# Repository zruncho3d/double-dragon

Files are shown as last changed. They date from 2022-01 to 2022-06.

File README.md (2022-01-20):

# Double Dragon

a Voron Zero mod to add Independent Dual Extrusion (IDEX).  "X0" for short.  **Now printing!**

**X0** adds a second printhead to a [V0](https://vorondesign.com/voron0.1) to enable multi-color prints, multi-material prints, and even overhangs atop dissolvable supports.  

*This repo includes everything you need to build your own X0, including CAD and STLs for printed parts, DXFs for panels, a list of parts, and a sample Klipper config.*  The .STEP file is now in the repo too.

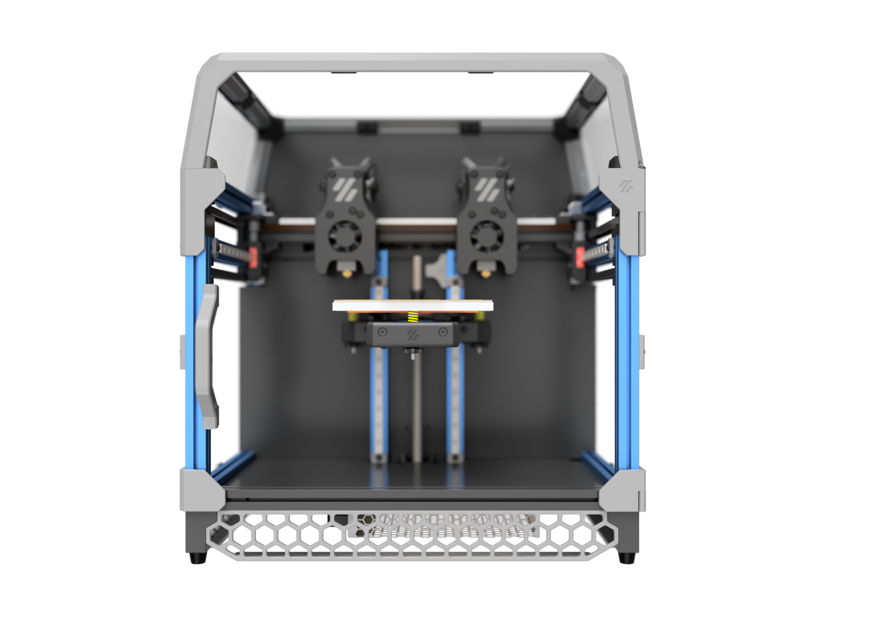
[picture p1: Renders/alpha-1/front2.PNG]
front


## Updates
* **2022-01-02** First multi-extruder prints!  See the alternating-copper-and-brass print below.
* **2022-01-01** See [this Reddit discussion](https://www.reddit.com/r/VORONDesign/comments/ru64ti/idex_v0_bad_idea_or_terrible_idea/) for reactions to the concept: bad idea, or terrible idea?
* **2021-12-31** Initial alpha-1 release!  This one was fun.  Came together quickly, too.

## Alpha-1 Release 2021-12-31

front

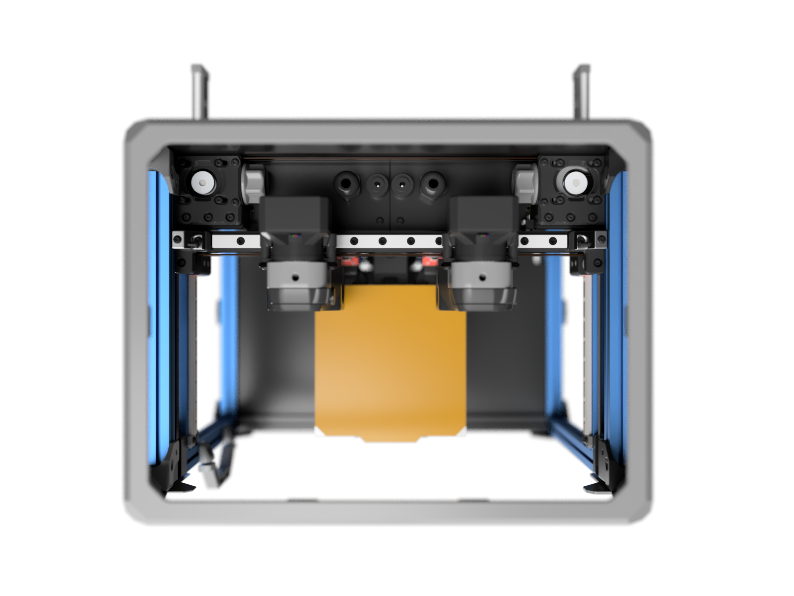
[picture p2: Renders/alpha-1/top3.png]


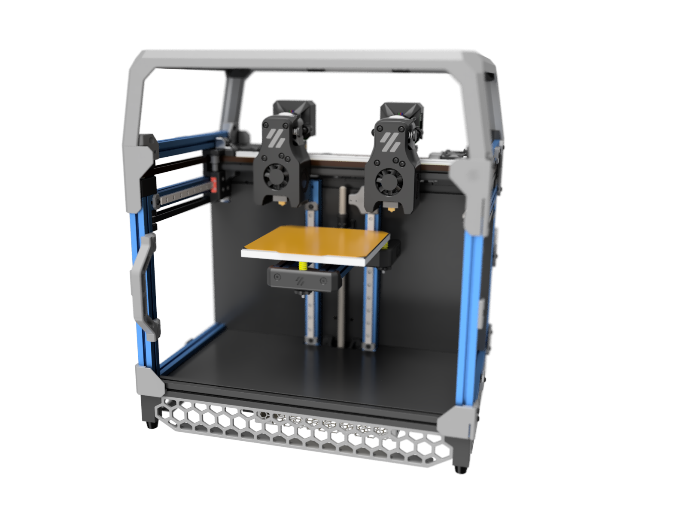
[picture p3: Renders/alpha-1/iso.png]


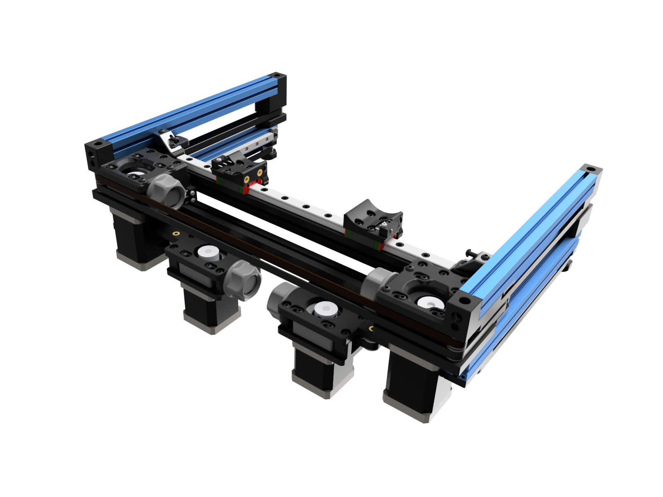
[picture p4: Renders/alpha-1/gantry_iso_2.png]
gantry iso


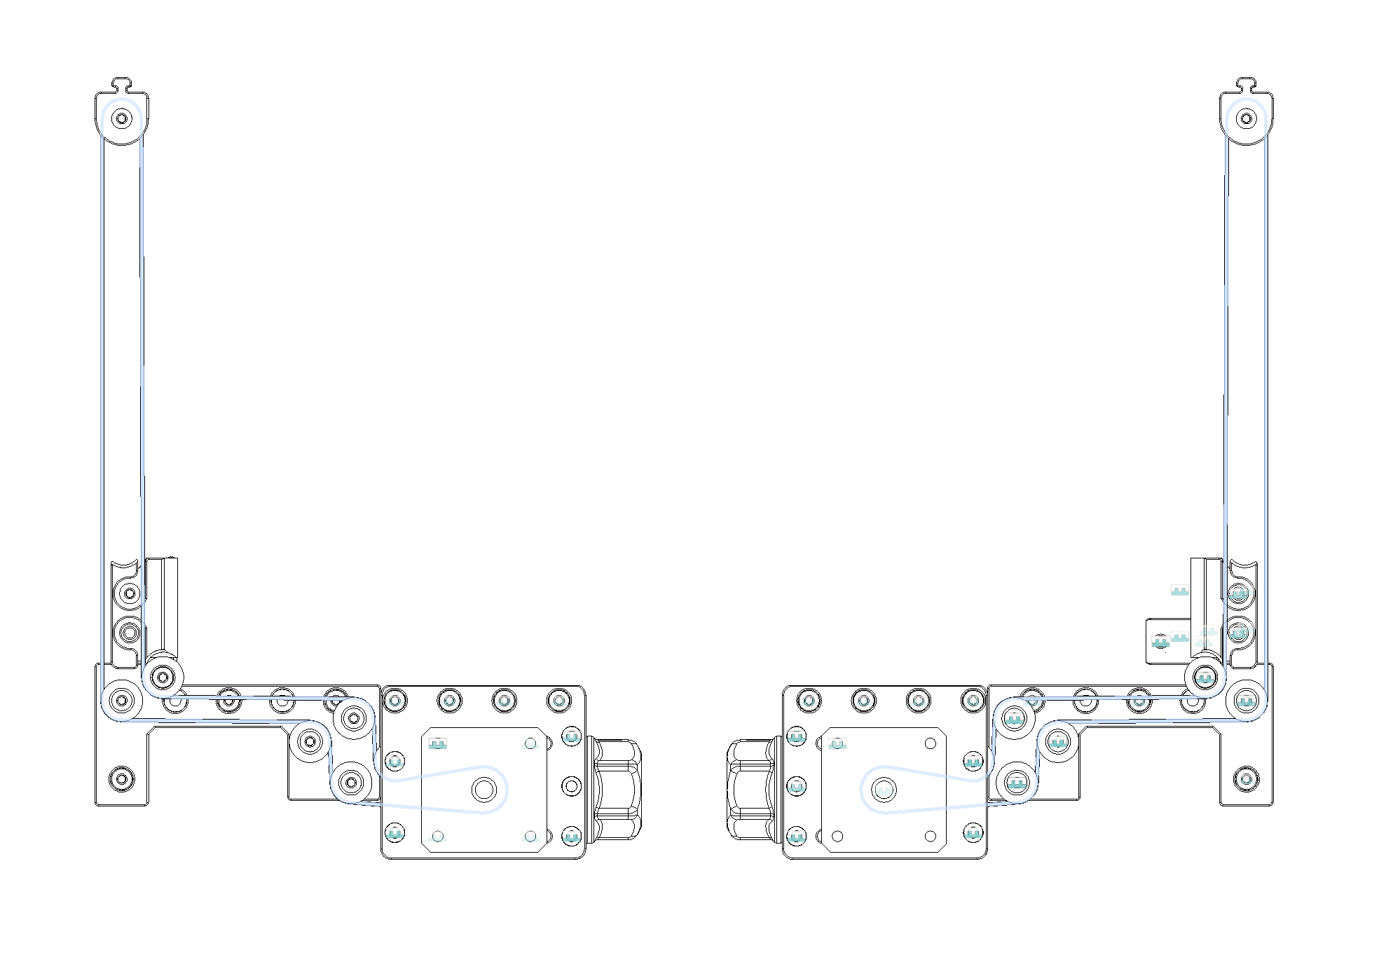
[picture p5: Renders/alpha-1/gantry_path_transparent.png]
gantry path


### Yes, it's real, and yes, it prints.  X0.000 in progress:

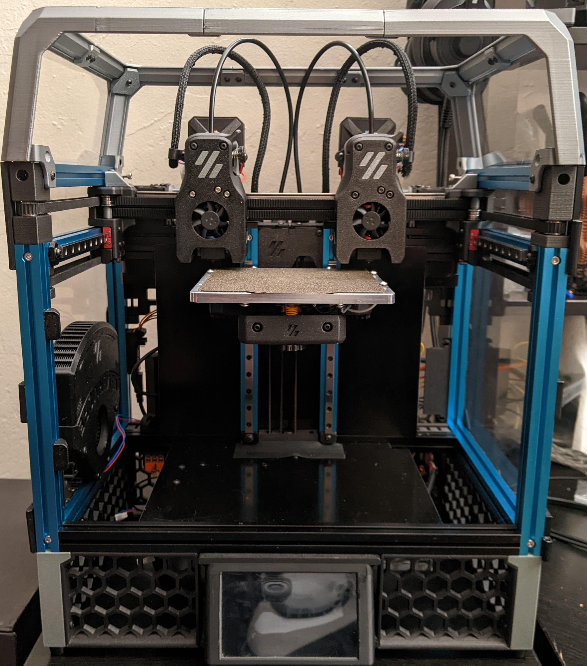
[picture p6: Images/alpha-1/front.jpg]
front


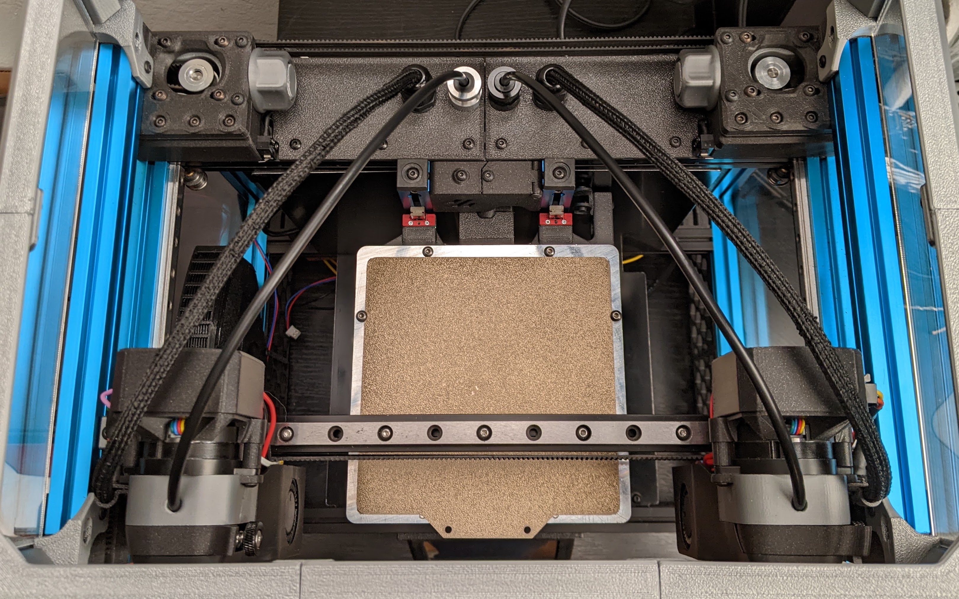
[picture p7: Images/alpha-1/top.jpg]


Sample print with two extruders in one part, with brass and copper PLA.

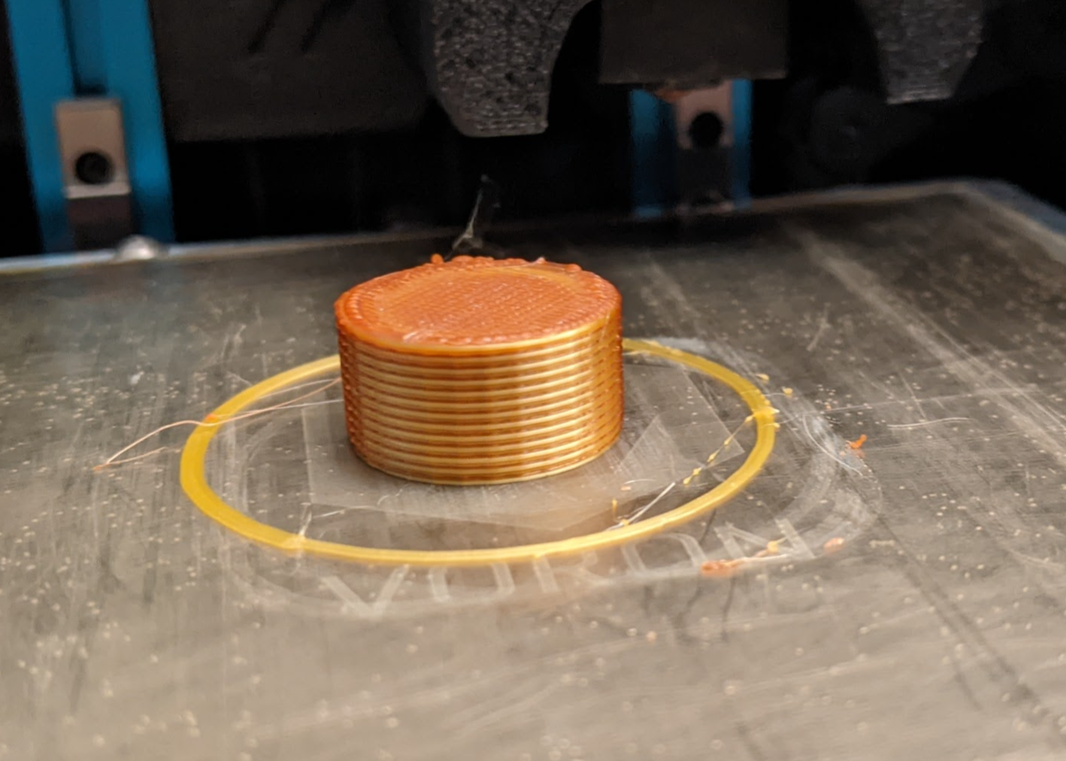
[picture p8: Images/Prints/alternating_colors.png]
alternating


Videos coming soon.

### Fun parts

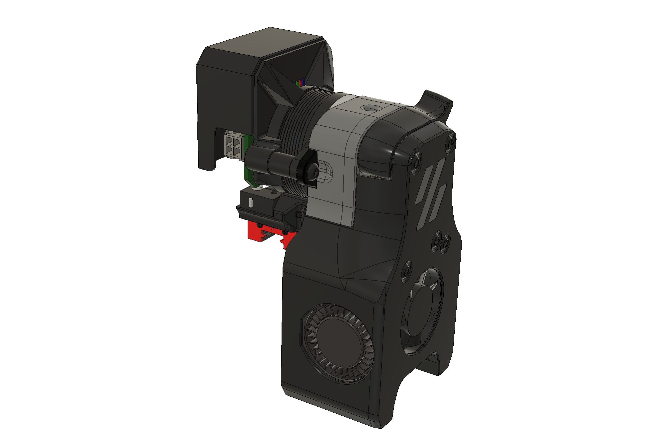
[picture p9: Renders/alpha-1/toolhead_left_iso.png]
Toolhead


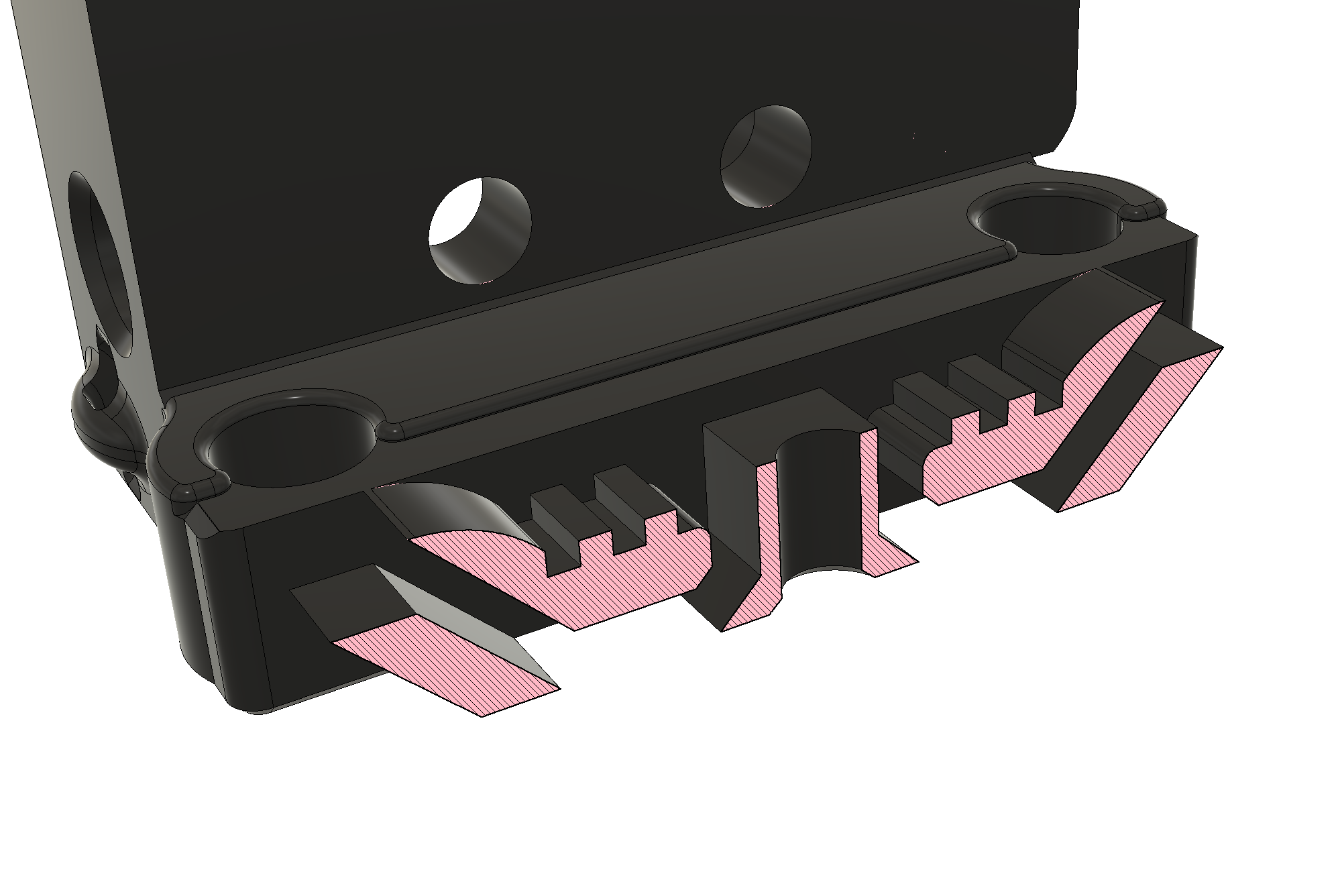
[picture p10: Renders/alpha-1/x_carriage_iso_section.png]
X Carriages iso section


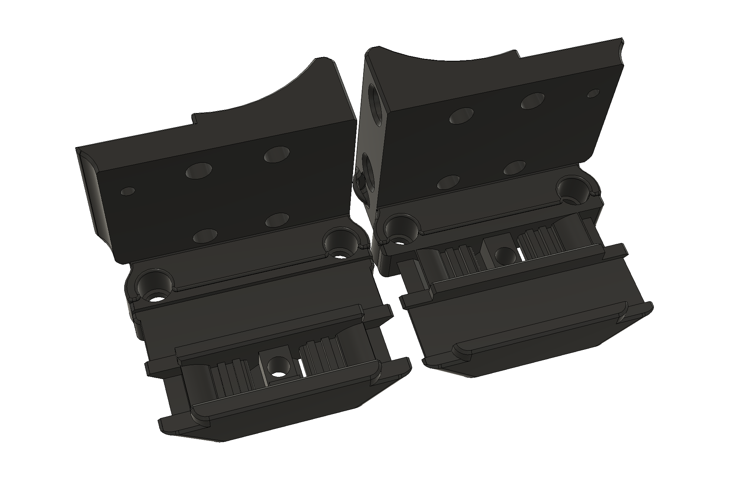
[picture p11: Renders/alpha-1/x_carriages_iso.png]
X Carriages iso


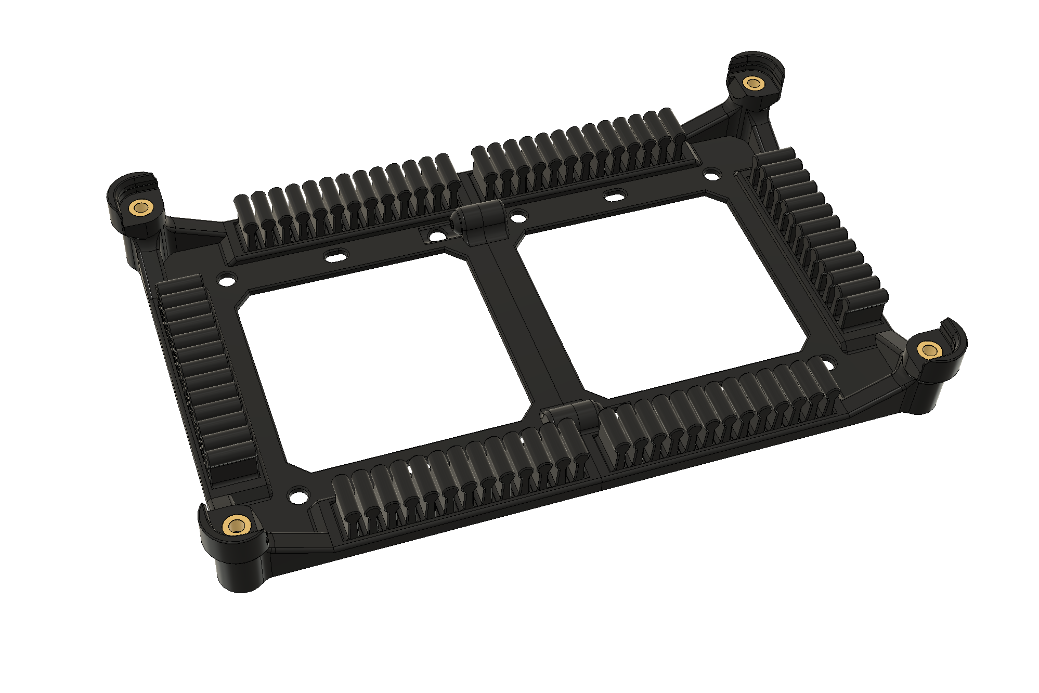
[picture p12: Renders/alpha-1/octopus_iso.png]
Octopus iso


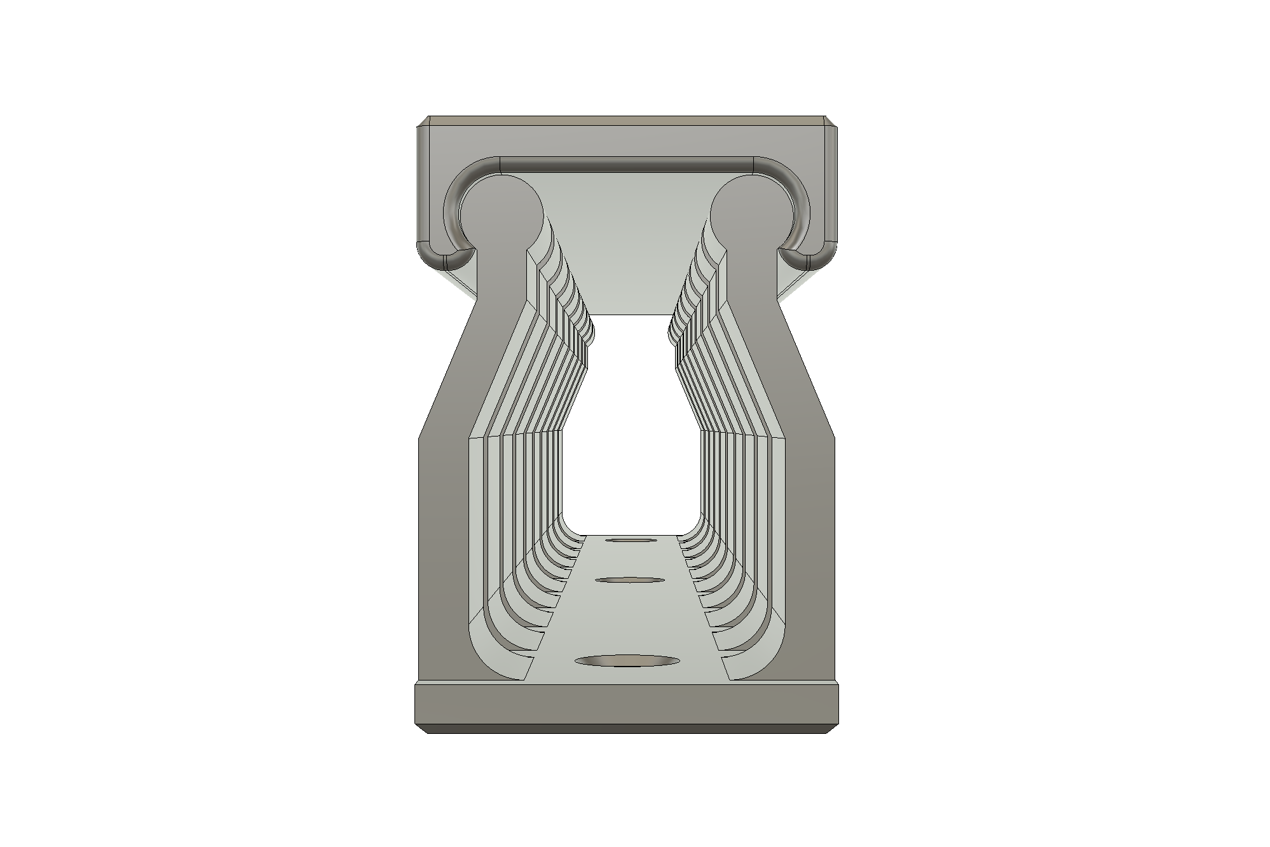
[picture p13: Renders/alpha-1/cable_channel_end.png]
Cable Channel End


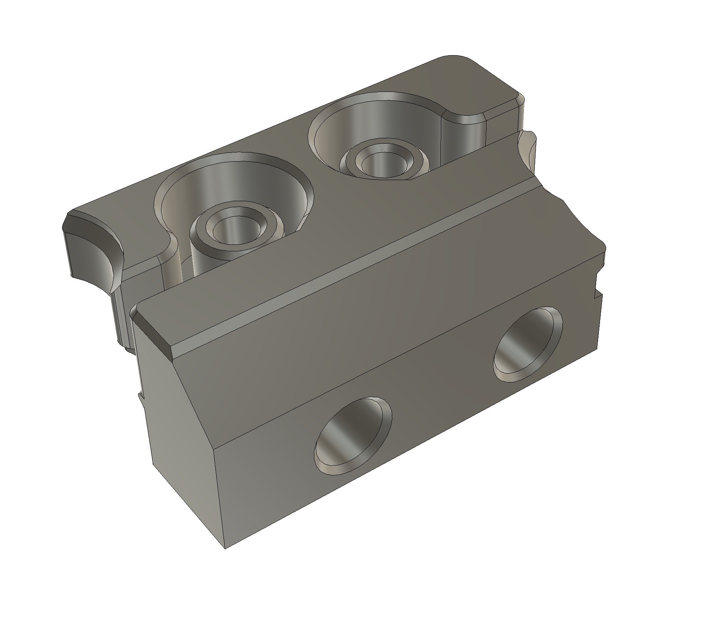
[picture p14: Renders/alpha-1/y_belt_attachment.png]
Y Belt Attachment


## I'm interested. What do I need to do?

Take a V0, then..

#### Double up the toolheads
You'll need a second toolhead.
* A default [V0.1 Mini Afterburner toolhead](https://github.com/VoronDesign/Voron-0/tree/Voron0.1/STLs/Toolheads/Mini_Afterburner) works fine, but anything V0-X-carriage-compatible will work too, like the [Mini AfterSherpa](https://github.com/KurioHonoo/Mini-AfterSherpa), which has some nice features.
* Toolhead boards are highly recommended, whether with-chip like the [Huvud](https://github.com/bondus/KlipperToolboard) or chip-less ([Pancake Board](https://github.com/christophmuellerorg/voron_0_pancake_board), [Timmit's V0 Umbilical](https://github.com/VoronDesign/Voron-Hardware/tree/master/V0-Umbilical), …).
* Anything that changes the X carriage will NOT work, such as the [Mini After-LGX-lite](https://www.bondtech.se/2021/12/27/voron-v0-1-toolhead-setup-for-lgx-lite/), at least until any changes are ported over.

#### Widen all the things!
* **100mm-wider extrusions** - 4x 300mm; [MakerBeamXL](https://www.amazon.com/MakerBeam-XL-Anodized-300x15x15mm-Pieces/dp/B06XJ5G5QY), Misumi, or whatever you prefer.  Or, keep the colorful extrusions from a kit and augment with 8x 50mm extensions, joined by M3 threaded rods, 3mm shafts, or long M3 screws.
* **100mm-longer X rail (250mm)** - a medium preload MGN9 rail with two MGN9C carriages is recommended, as it reduces the potential for toolhead wobble.  Ask the seller for medium preload at purchase time and ask them to put both carriages on the rail.  Make sure to order two carriages!  [CNA rail and carriages on AliExpress](https://www.aliexpress.com/item/32773296501.html?spm=a2g0s.12269583.0.0.4ea2494dwPIVR2)
* **100mm-plus wider bed (optional)** - see notes below.
* **100mm-wider panels (optional)** - see DXFs folder and image below.  You can ignore these if the printer is unenclosed, or you can make printed 50-mm-wide shim parts, possibly with a nice accent color.  The tophat panels are a bit harder to extend, but you could shim these too, potentially.
* **100mm-wider skirts (optional)** - this repo includes a 100mm hex skirt to match the [default V0.1 skirts](https://github.com/VoronDesign/Voron-0/blob/Voron0.1/STLs/Skirt_x3.STL). X0.000 above has custom 70mm skirts to fit a [4" touchscreen mod](https://github.com/Fleafa/VoronUsers/tree/V0.1-Trident-skirt/printer_mods/roboticator24/4inch_touchscreen_mount_for_v2.4) for [KlipperScreen](https://github.com/jordanruthe/KlipperScreen).  But again, use what you like, such as [MCMBen's Trident-style skirts](https://github.com/Fleafa/VoronUsers/tree/V0.1-Trident-skirt/printer_mods/MCMBen/Voron0_Trident_Skirt), which nicely integrate the mini V0 display you may already have.

The panel order looks like this, from SendCutSend:

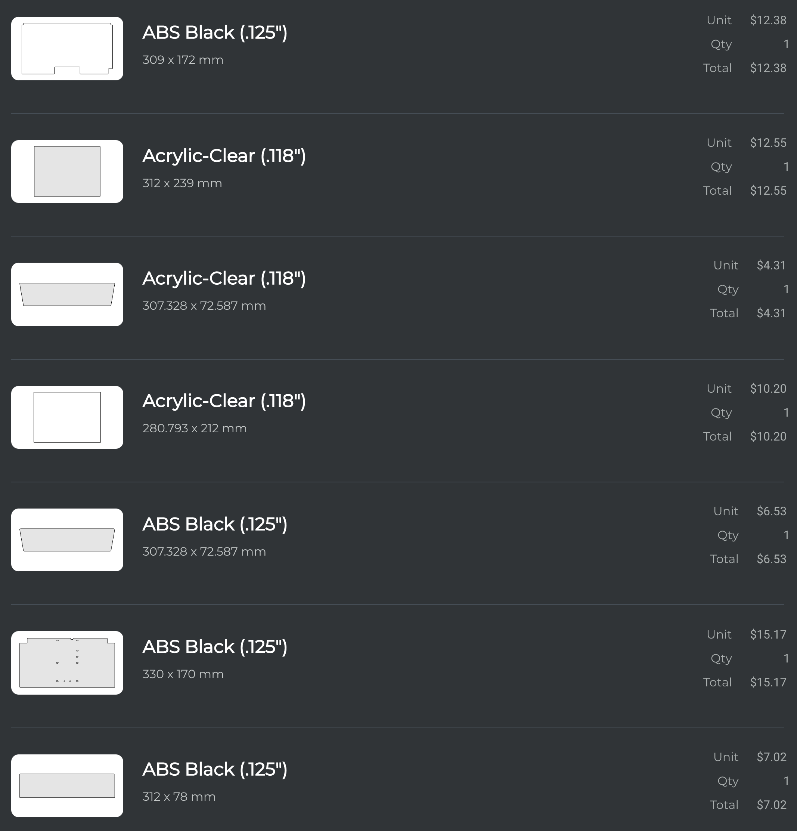
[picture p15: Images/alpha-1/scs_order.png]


#### Add more drives!
This mod uses two Y motors for simplicity in a `hybrid-corexy` config.  You'll need:
* **Belts**: +N 6mm-width GT2 belt; can reuse your now-too-short belts on the Y drives.
* **Pulleys**: +2 20-tooth GT2
* **Endstops**: +2 Omron D2F switches
* **Bearings**: +28 F623 bearings (sorry for the number... had to fit the existing V0 footprint)
* **Motors**: +2 NEMA14 for the Y drives.  If using full-length 48mm+ motors, an Octopus will not fit the provided mount, but a Spider will.  V0.0-stock motors are shorter and will fit.
* **M3 Screws**: Yes, all BHCS; includes at least M3x6, M3x8, M3x10, M3x12, M3x16, M3x20, M3x25.
* **M3 Nuts**: Yes
* **M3 Heatsets**: Yes
* **M3 Washers**: Yes

Note, parts above are *just* for drives, not for the toolhead.  Those will add to the bill of materials.

Also: **additional stepper driver ports**.  Octopus, Spider, Fly, GTR, S6, 2x SKR Mini/Pico, … Klipper doesn’t care.  Use whatever you’ve got that gives you added ports.  You need an extra 2 stepper ports for Y motion and one extra stepper port for the second extruder, unless you go with a toolhead board.

#### More power!!!  

The extra power draw of three more steppers, plus an extra toolhead heater, **absolutely** requires a more capable power supply than a stock V0, whether 100W for an AC bed or 150W for a DC bed.  DO NOT run without known margin.  If you're not sure, buy or borrow an inline power meter to confirm.

A second power supply or larger one both will work fine.  The good news is that you have 100mm additional width to fit it below the main deck panel.

Consider a UHP200, dual LRS-100-24 units (what I use), an LRS-350-24 if you don't mind occasional fan noise, an LRS-150-24 with an AC bed, or really, anything else.

There’s no BOM yet, because there’s only two new parts for the BOM - the longer rail and the longer extrusions.

#### Printed parts (required)

Most of the bigger parts are *fully reused* from a V0.  That’s kinda the point here… take a V0 and make it an IDEX with the fewest modifications possible.  That includes the toolhead, AB blocks, front idlers, top gantry parts, and enclosure parts.

What remains?  You’ll need a few new parts, plus a few copies of existing V0 parts.  But surprisingly, not that much.  Everything is printable on the 120x120 bed of a V0.

| Category | Part | Qty | Notes |
| - | - | - | - |
| X Gantry | ```XY_Joint_Lower_Extended``` | 1 + 1 | Enables attachment to Y belt blocks |
| | ```X_Endstop``` | 1 + 1 | Enables tightening + tensioning without screw interferences |
| | ```X_Carriage``` | 1 + 1 | Needed to support belt passthrough for hybrid-corexy layout; leaves extra belt around, so it improves the experience of tightening/retightening |
| Y Drives | ```Y_Belt_Attachment``` | 1 + 1 | Perfect fit with the Y drive pulleys to enable 120mm Y travel
| | ```Y_Front_Idler_Mount``` | 4 | Spaces and retains Y front idler bearings |
| | ```Y_Bearing_Plate``` | 1 + 1 | Holds bearings to route the belts |
| | ```Y_Drive_Frame_Upper``` | 1 + 1 | Shortened and modified V0 part |
| | ```Y_Drive_Frame_Lower``` | 1 + 1 | Shortened and modified V0 part |
| | ```Y_Drive_Tensioner``` | 2 | Shortened and modified V0 part |
| | ```Tensioner_Knob``` | 2 | [Extra of a stock V0 part](https://github.com/VoronDesign/Voron-0/blob/Voron0.1/STLs/%5Ba%5D_Tensioner_Knob_x2.stl) |
| Misc | ```Spool_Holder``` | 1 | [Extra of a stock V0 part](https://github.com/VoronDesign/Voron-0/blob/Voron0.1/STLs/Spool_Holder_V0_x1.STL) |

#### Printed parts (modified)

The left-side AB block needs one modifiecation: to drill two sub-2mm holes in the existing part to match the other side, then use 2x self-tapping M2 screws to attach it.

#### Printed parts (optional)

| Category | Part | Qty | Notes |
| - | - | - | - |
| Wire Management | ```Separator``` | 1 + 1 | Full-width covers to connect toolhead to [cable glands](https://www.amazon.com/gp/product/B077R1RT2T) and reverse bowden tubes
| | ```Reverse_Bowden_Clip``` | 2 | Clamps to a 4mm bowden tube and mounts to Dragon groovemount
| | ```Cable_Channel_100mm_15x22_Base``` | 3 | Keep those wires organized
| | ```Cable_Channel_100mm_15x22_Cover``` | 3 | Keep those wires organized
| | ```Octopus mount base``` | 2 | Rotationally symmetric part to hold Octopus
| | ```Wire_Fingers``` | 6 | Clips into Octopus mount, but also usable with a piece of VHB tape below
| Tophat | ```Tophat_Middle_Spacer``` | 2 | Widens tophat by 100mm
| | ```Front_and_Rear_Midclip``` | 2 | [Extra of a stock V0 part](https://github.com/VoronDesign/Voron-0/blob/Voron0.1/STLs/Tophat/Front_and_Rear_Midclip_x2.STL)
| Skirts | ```Skirt_Center``` | 1 | Matches stock V0.1 front skirts

See also toolhead parts in the ```Huvud_Toolhead``` folder.  Quantities for those parts assume you go for 2.

All parts should be printed at standard Voron settings (4 perims, 40% infill, 5 top / 5 bottom layers) except for:
* ```Wire_Fingers```: use 2 perims, 0% infill, 0 top / 0 bottom layers - they’re meant to be flexible loops
* ```Tophat_Middle_Spacer```: use 0.16 layers, as the overhangs are significant

All parts should already be in print-ready orientation, where the seam is assumed to be at the back (+Y).  

No supports are necessary for any parts.

### Software. How?

X0 uses a stock mainline Klipper with minimal changes.  Duplication and mirroring may require extra patches; those are currently untested.  There’s a sample Octopus config in the repo.  The key changes to Klipper config are to define a second Y drive and use ```[dual_carriage]``` to define a second X drive.

Also, make sure your slicer outputs T0 and T1 commands; for SuperSlicer, select the Marlin type, not Klipper type.  The easiest way to test this is to right-click the bottom right of the slicer view in SuperSlicer and have it do a pattern of alternating extruders.  You’ll need to have the two extruders configured too, but they should be identical.

### Calibration.  How?

Great question.  Welcome to the bleeding edge.  It’s sharp.

The best guide I’ve seen is this [guide](https://github.com/Klipper3d/klipper/pull/4508/commits/f2cfa7021d2f2079829e65b9544e9c80def937d6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) from charlespick on Github.
You print test patterns to align the two toolheads in X and Y, then test until Z is right.  Here’s a sample.

### What part size can I print?

Good question.

If you keep a V0 120x120 bed, then _most_ of the V0 printable size remains.  The V0.1 MiniAB is 53mm and the added travel is 50mm… so one carriage would hit the other at 3mm from the build-plate edge.  That means you can print a single part with two materials or colors, up to 114mm in X and ~120mm in Y.  Great!

But remember: toolheads can’t touch.  So in mirror mode (which requires toolhead height adjustment; not implemented yet), you lose that 53mm between nozzles, yielding 2 parts at 33.5mm x 120mm.  In Duplication mode, you get the space divided by two, up to the toolhead edge - 60mm x 120mm for each part.  Much better.

But what if you go with a larger bed?

You can print much wider, and that changes the utility of your V0 in a big way.   Assume a 100mm-wider 220mm bed width, or more.  In mirror mode, you lose 53mm again, so you get 2x 83.5mm x 120mm [(220.0 - 53)/2].  Much better.  In Duplication you get the space divided by two - 110mm x 120mm for each part.

That's pretty good.  That's why toolhead height adjustment would be a great improvement.

### Can I use [insert V0 mod here]?

Maybe.  

The Double Dragon mod is compatible with many Z mods for V0, including [Tri-Zero](https://github.com/zruncho3d/tri-zero) for automatic bed leveling, as well as various belted Z conversions, including:
*  MCMBen's  [Block-and-Tackle Z](https://github.com/Fleafa/VoronUsers/tree/master/printer_mods/MCMBen/Voron0_Block_and_Tackle_Z_Belt/STLs)
* nhchiu's [Movable Pulley Z](https://github.com/nhchiu/VoronUsers/tree/pulley_z/printer_mods/nhchiu/V0.1_Movable_Pulley_Z)
* theFPVgeek's [belted Z mod](https://github.com/theFPVgeek/VoronUsers/tree/master/printer_mods/theFPVgeek/v0-zbelt-mod)
* MathematicalPotato's [V0.1 mod of theFPVgeek's mod](https://github.com/VoronDesign/VoronUsers/tree/master/printer_mods/MathematicalPotato/v0.1_belted_z_drive)
* ... and more

Lights on top should be fine.  Tophat lifters may need some extensions for the added width.  Also, the Y belts below the side extrusions might get in the way of some mods though, so watch out.

###  What’s left to do?

Lots of stuff.  You’ve got the CAD.  Have at it.  

Here’s a starter list of useful contributions.  PRs welcome!
* Mechanical nozzle height adjustment on the toolhead; required to do mirror and duplicate modes correctly.
* Purge bucket
* Nozzle scrubber
* Narrower toolhead for more usable X
* Calibration assists
* Printable rear separator parts to fit the 14-pin connectors of no-chip toolhead boards
* Printable panel extensions

### Questions.  Where?

Project development and updates live in the ```#double-dragon``` channel in the [DoomCube Discord](https://discord.gg/doomcube).

Feel free to report issues as GitHub issues!  Makes them easier to track.

**What am I seeing in the pictures?  That doesn't match the CAD.**

Good eye.  You can modify a stock V0.1 with the mods listed above and you'll see something like the renders, but the images are a bit different.

X0.000 in the pics has a few tweaks to a stock V0.1, in addition to Double Dragon-specific mods:

* MCMBen's [Block-and-Tackle Z for V0](https://github.com/Fleafa/VoronUsers/blob/master/printer_mods/MCMBen/Voron0_Block_and_Tackle_Z_Belt/STLs/%5Ba%5D_tensioner_v1.stl)
* 2x Custom Rotating Spool holders
* 2x Huvud mounts for small NEMA17 motors, with custom cable clips, plus connectors to pass 5V to the MiniAB fan.  Only 5 wires each.
* 2x Repurposed Dragon groovemount adapters for bowden tubes
* Custom 70mm skirts to fit a 4" touchscreen mod for KlipperScreen
* FUNCORE [accessible-screws V0.1 frame](https://www.aliexpress.com/item/1005003198676826.html?spm=a2g0o.9042311.0.0.39c74c4dcDSi6v)

**The name. Why?**

90s nostalgia + “it literally uses two Dragon hotends” + makes clear it’s an IDEX.  

But DD could mean Direct Drive, so just call it X0 for short.

### Credits

* **@eddietheengineer**
  * [Eddie's IDEX walkthrough video](https://www.youtube.com/watch?v=31fqpKYj7v4) is *the reason this mod exists*.  Watch it.  It lays out the approach of modifying a CoreXY printer to add a second extruder, without moving the belt paths. If a V0 is your lego kit, this is a new model you can build by combining two of the same set.
  * [Tridex](https://github.com/FrankenVoron/Tridex/) is the cleanest and most awesome IDEX I’ve seen.  9 steppers?!?  Yeah.  Squint.. and Double Dragon may look just like this, in combination with the [Tri-Zero mod](https://github.com/zruncho3d/tri-zero).
  * [Doom IDEX](https://github.com/FrankenVoron/IDEX) - a preceding Voron IDEX.
* **@nemgrea** This mod is probably 85-90% unmodified V0 content, so nemgrea gets a ton of credit for driving the V0 design here.  The Y blocks are chopped V0 AB blocks.  If it ain’t broke, don’t fix it.  Or, fix it until it’s broken… which one is it again?
* **@ankurv** A badass [Switchwire IDEX](https://www.youtube.com/watch?v=k3Mkut2jhwM) and long conversation provided motivation.
* **@hartk1213**  The carriages derive from [hartk's MGN9C mod](https://github.com/VoronDesign/VoronUsers/tree/master/printer_mods/hartk1213/Voron0_MGN9C_X_Axis).

### Project Timeline

* 2021-12-31 Initial alpha-1 release
* 2021-12-26 After building, wiring, and configuring... first calibration prints.
* 2021-12-12 All gantry parts designed, printed, and assembled, including X carriages.
* 2021-12-04 This is actually going to happen! V0.562 gets torn down, to be reborn as an IDEX with a blue frame.
* 2021-11-27 Y motor strategy figured out, designed & printed.
* 2021-11-25 Y belt path mocked up.  This may not be so crazy...  
* 2021-11-23 Initial half-baked concept formed.  Channel request denied.  Provides motivation to make something channel-worthy. Discovered [Eddie’s IDEX walkthrough](https://www.youtube.com/watch?v=31fqpKYj7v4), which provides clarity as to how this might work.

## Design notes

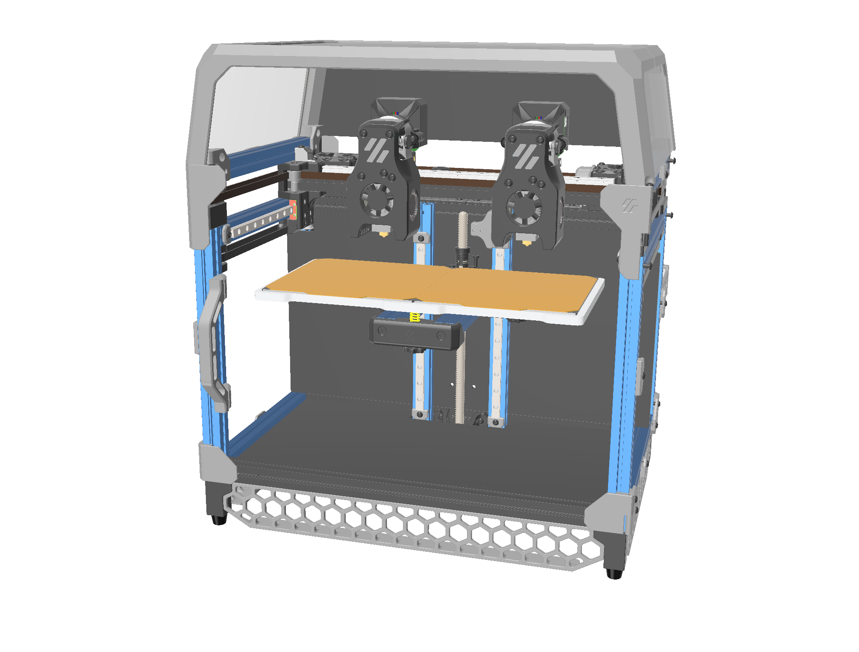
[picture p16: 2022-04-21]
Renders/doublewide.png

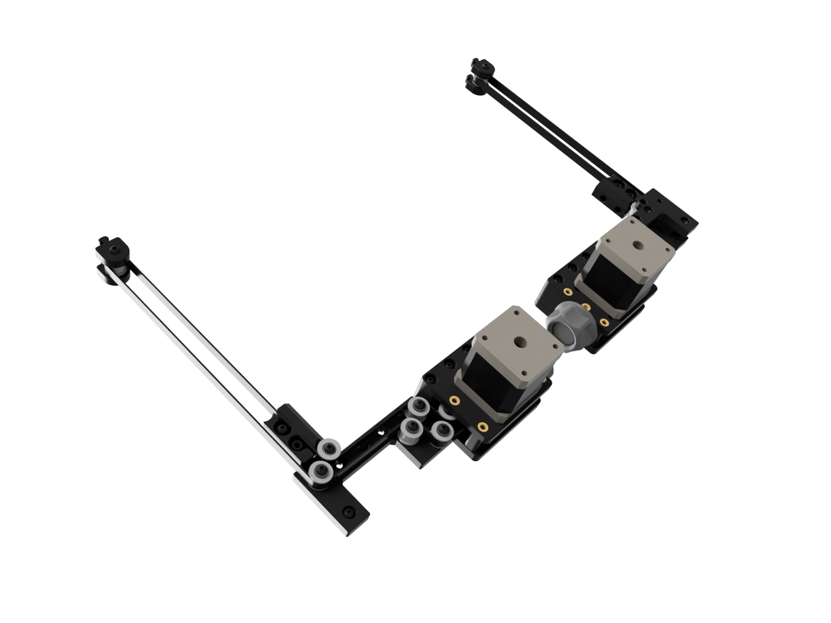
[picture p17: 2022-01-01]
Renders/alpha-1/y_drives_perspective_3.png

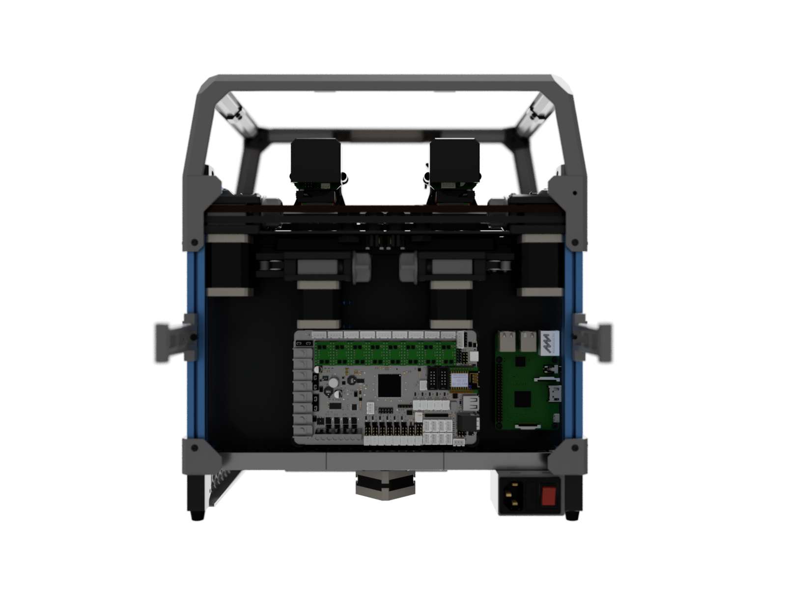
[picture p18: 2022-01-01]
Renders/alpha-1/rear.png

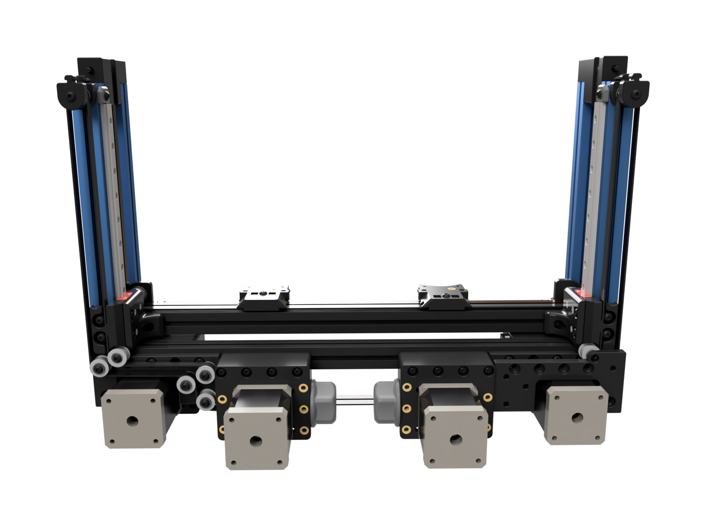
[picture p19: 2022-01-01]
Renders/alpha-1/y_drive_rear_perspective_2.png

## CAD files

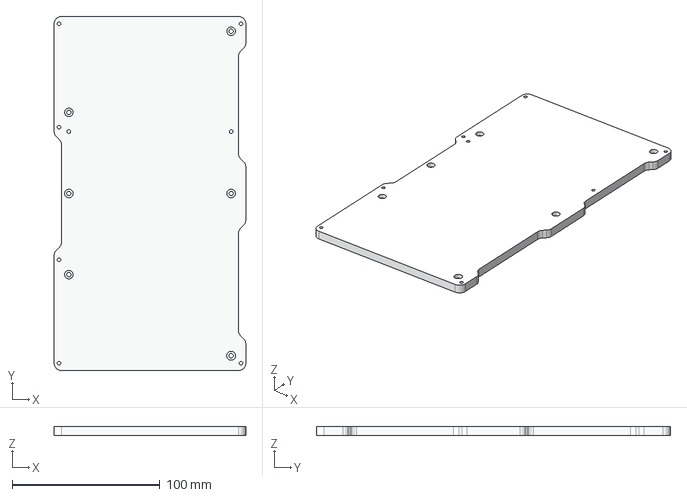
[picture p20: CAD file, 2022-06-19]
CAD/Dragon_Bed_240.step
130.0 x 240.0 x 6.15 mm

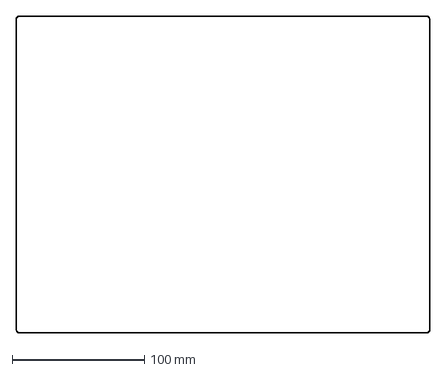
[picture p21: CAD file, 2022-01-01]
DXFs/Widened_Front_Panel_x1.dxf
312.0 x 239.0 mm

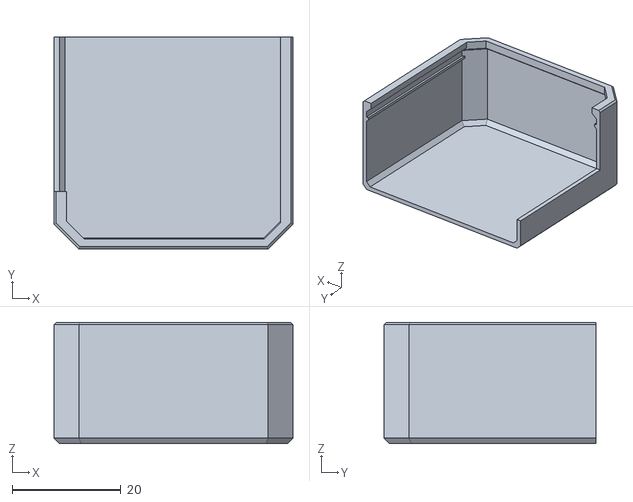
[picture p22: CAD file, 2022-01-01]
STLs/Huvud_Toolhead/Huvud_Shroud_Right_x1.stl
44.0 x 39.0 x 22.3

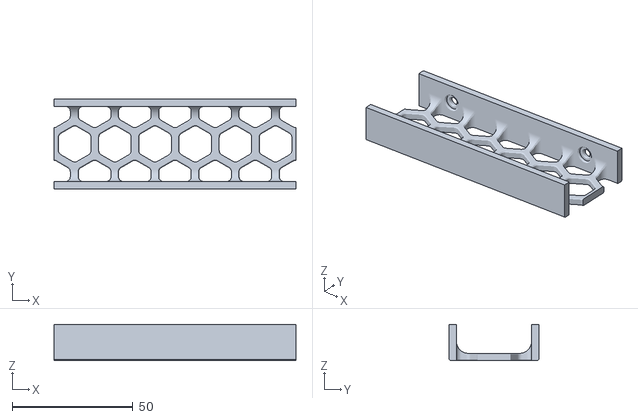
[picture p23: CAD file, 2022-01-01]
STLs/Optional/Skirt_Center_x1.stl
100.0 x 37.0 x 15.0

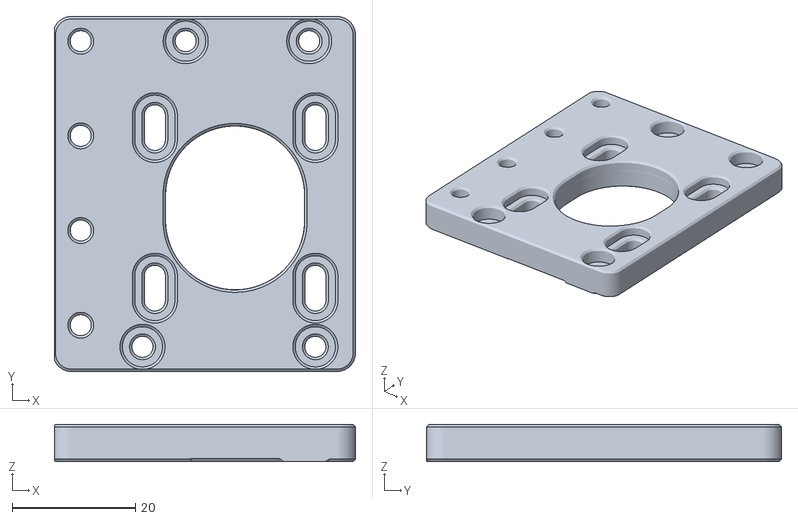
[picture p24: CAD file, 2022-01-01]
STLs/Y_Drive_Frame_Upper_Left_x1.stl
48.8 x 57.5 x 6.00

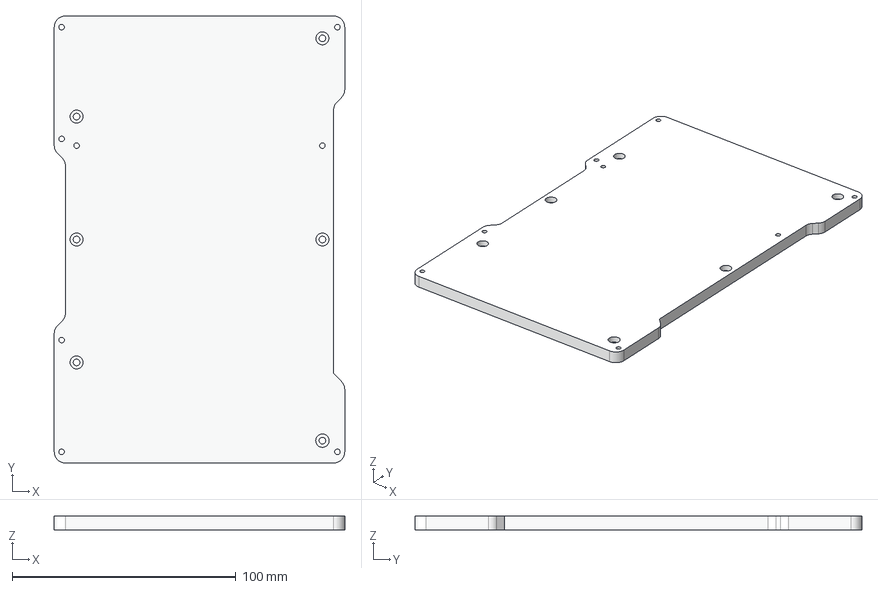
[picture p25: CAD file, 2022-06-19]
CAD/Dragon_Bed_200.step
130.0 x 200.0 x 6.15 mm

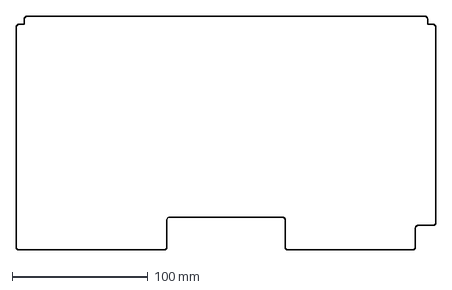
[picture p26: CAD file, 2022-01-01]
DXFs/Widened_Deck_Panel_x1.dxf
309.0 x 172.0 mm

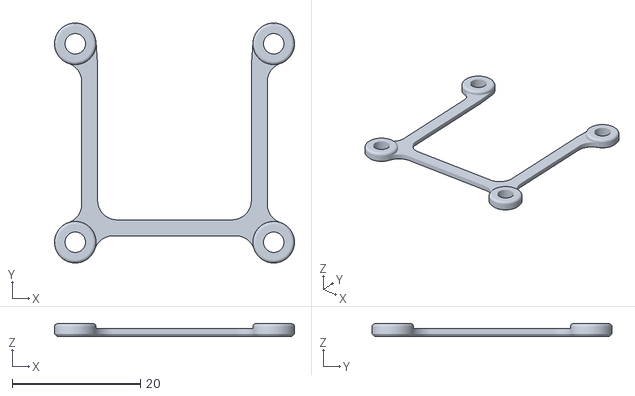
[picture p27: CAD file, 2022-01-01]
STLs/Huvud_Toolhead/Huvud_Spacer_x2.stl
37.5 x 37.5 x 2.00

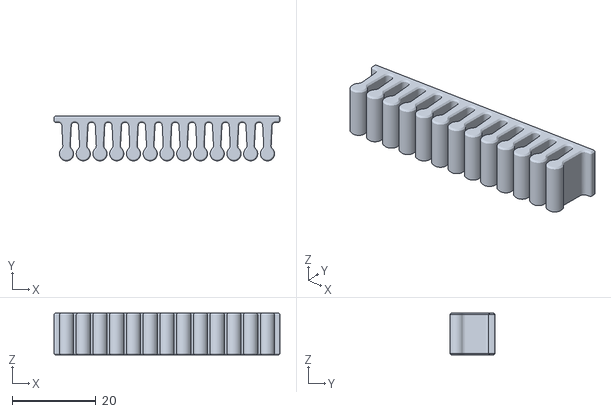
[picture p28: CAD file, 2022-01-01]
STLs/Optional/Wire_Fingers_x6.stl
54.0 x 10.7 x 10.0

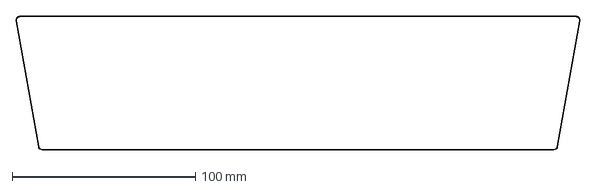
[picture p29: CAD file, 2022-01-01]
DXFs/Widened_Front_Rear_Tophat_Panel_x2.dxf
307.5 x 72.6 mm

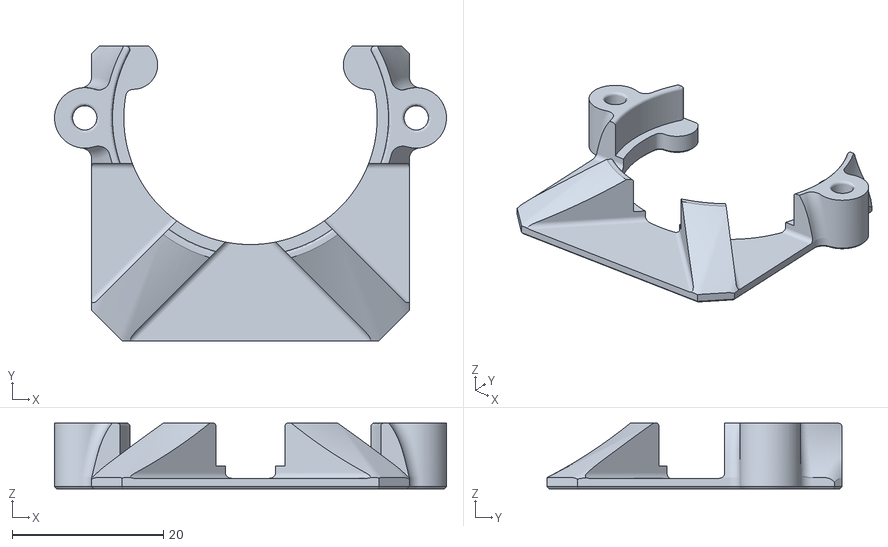
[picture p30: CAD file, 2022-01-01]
STLs/Huvud_Toolhead/Huvud_Mount_x2.stl
51.8 x 39.0 x 8.70

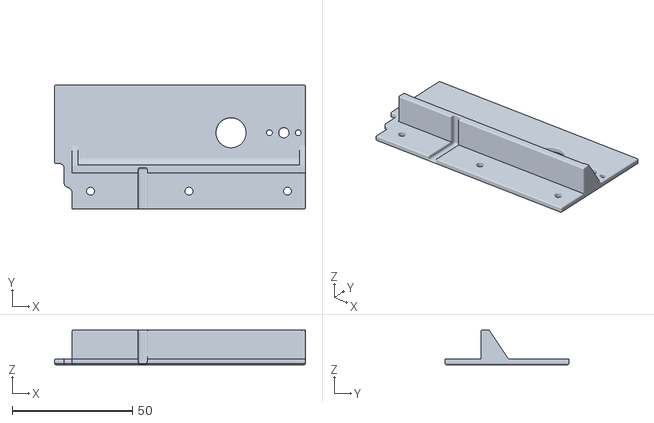
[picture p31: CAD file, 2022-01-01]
STLs/Optional/Separator_Right_x1.stl
104.5 x 51.8 x 14.5

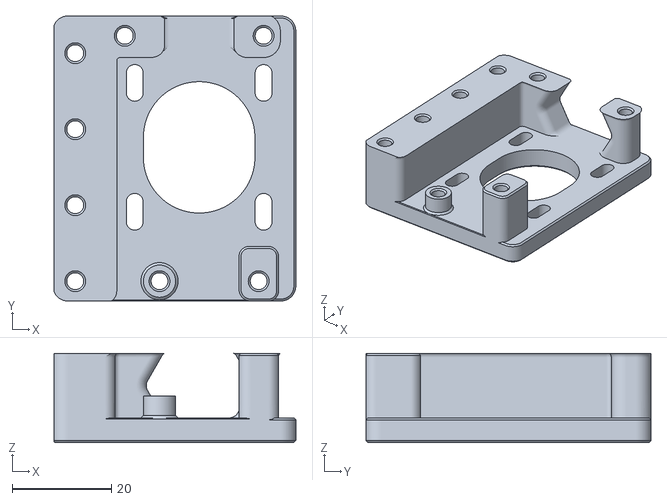
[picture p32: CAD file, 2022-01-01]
STLs/Y_Drive_Frame_Lower_Right_x1.stl
48.7 x 57.5 x 18.0

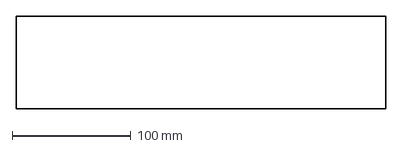
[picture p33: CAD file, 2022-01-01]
DXFs/Widened_Rear_Short_Panel_x1.dxf
312.0 x 78.0 mm

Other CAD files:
STLs/Y_Drive_Frame_Upper_Right_x1.stl
STLs/Huvud_Toolhead/Huvud_Motor_Spacer_x4.stl
STLs/Optional/Separator_Left_x1.stl
STLs/Y_Belt_Attachment_Left_x1.stl
CAD/Dragon_Bed_200.f3d
CAD/Dragon_Bed_240.f3d
DXFs/Widened_Mid_Panel_x1.dxf
DXFs/Widened_Top_Tophat_Panel_x1.dxf
STLs/Huvud_Toolhead/Huvud_Shroud_Left_x1.stl
STLs/Optional/Cable_Channel_100mm_15x22_Base_x3.stl
STLs/Optional/Cable_Channel_100mm_15x22_Cover_x3.stl
STLs/Optional/Octopus_Mount_Base_x2.stl
STLs/Optional/Reverse_Bowden_Clip_x2.stl
STLs/Optional/Tophat_Middle_Spacer_x2.stl
STLs/XY_Joint_Lower_Extended_Left_x1.stl
STLs/XY_Joint_Lower_Extended_Right_x1.stl
STLs/X_Carriage_Left_x1.stl
STLs/X_Carriage_Right_x1.stl
STLs/Y_Bearing_Plate_Left_x1.stl
STLs/Y_Bearing_Plate_Right_x1.stl
STLs/Y_Belt_Attachment_Right_x1.stl
STLs/Y_Drive_Frame_Lower_Left_x1.stl
STLs/Y_Front_Idler_Mount_x4.stl
STLs/[a]_X_Endstop_Left_x1.stl
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

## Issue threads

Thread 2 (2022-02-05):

Front Idler height

harry-boe, 2022-02-05:
Pleas reduce the height of the front idler by  0.2mm

Frame extrusion do not longer align when used with a Z front rail for the Try-Zero mod.
It might as well improve the threads on the m3x25 mounting screw.

harry-boe, 2022-02-06:
I changed the design an lowered them by 0.2 mm
with the new printed parts i get on side dead on the other still 0.1 mm off

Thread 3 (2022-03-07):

Wrong heatset insert size in tophat middle spacer

zruncho3d, 2022-03-07:
From BeastBc on Discord:

Middle spacer in the tophat has the wrong size holes for the heat set insert: it measures 5.7mm instead of 4.7 recommended

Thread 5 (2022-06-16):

Wider tophat panels a bit too much at 3mm

zruncho3d, 2022-06-16:
More here on DoomCube discord: https://discord.com/channels/825469421346226226/926920300816396320/987000852965367948

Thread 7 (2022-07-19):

Y Attachments break when removeing belts

skyne, 2022-07-19:
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

I've installed them in reverse, when realized and tried to remove the belts to swap them, the middle part broke out (see pic.)

Additional info:

- probably I've installed the covers with longer screws than intended
- I've also had white (reinforced, stiff) belts installed, this could've also caused the "harder to remove" effect

zruncho3d, 2022-07-19:
Oh, you definitely want to add screws here because the plastic parts are in shear.

This view of Red5's Tri-Zero shows what it should look like, with M3 screw (I think M3x8 or M3x6, would have to check CAD or measure)

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

bstrawsma, 2022-07-19:
I also modified this part when installing it on mine to have a through hole with a heat set insert on the back and then held in place with washers.

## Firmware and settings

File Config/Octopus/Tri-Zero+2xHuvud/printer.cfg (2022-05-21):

# This file contains common pin mappings for the BigTreeTech Octopus V1.
# To use this config, the firmware should be compiled for the STM32F446 with a "32KiB bootloader"
# Enable "extra low-level configuration options" and select the "12MHz crystal" as clock reference

# after running "make", copy the generated "klipper/out/klipper.bin" file to a
# file named "firmware.bin" on an SD card and then restart the OctoPus with that SD card.

# See docs/Config_Reference.md for a description of parameters.

[include mainsail.cfg]
[include toolhead0.cfg]
[include toolhead1.cfg]
#[include builtin_extruder0.cfg]
#[include builtin_extruder1.cfg]
[include my_macros.cfg]
[include AndrewEllisMacros.cfg]

[mcu]
##  Obtain definition by "ls -l /dev/serial/by-id/" then unplug to verify
##--------------------------------------------------------------------
# Starts as: serial: /dev/serial/by-id/usb-STMicroelectronics_BIGTREE_OCTOPUS_CDC_in_FS_Mode_204331844E53-if00
# After first build:
serial: /dev/serial/by-id/usb-Klipper_stm32f446xx_360012000650534E4E313120-if00
restart_method: command
##--------------------------------------------------------------------

[force_move]
enable_force_move: true

# Intentionally slow until limits are determined and stepper currents are set correctly.
[printer]
kinematics: hybrid_corexy
max_velocity: 200
max_accel: 2000
max_z_velocity: 100
max_z_accel: 200
square_corner_velocity: 5.0

#####################################################################
#   X Steppers
#####################################################################

##  Right Extruder X motor (when looking at the front)
##  Connected to MOTOR_0
##  Endstop connected to DIAG_0
[stepper_x]
step_pin: PF13
dir_pin: PF12
enable_pin: !PF14
rotation_distance: 40
microsteps: 32
full_steps_per_rotation: 200
# Uncomment below if using direct inputs on Octo
# endstop_pin: ^PG6#
endstop_pin: head0:PA1

position_min: 4
position_endstop: 169
position_max: 169

homing_speed: 50
homing_retract_dist: 3
second_homing_speed: 5
homing_positive_dir: true

[tmc2209 stepper_x]
uart_pin: PC4
interpolate: false
run_current: 0.7
hold_current: 0.5
sense_resistor: 0.110
stealthchop_threshold: 500

##  Left Extruder X motor (when looking at the front)
##  Connected to MOTOR_2
##  Endstop connected to DIAG_2
[dual_carriage]
axis: x
step_pin: PF11
dir_pin: PG3
enable_pin: !PG5
rotation_distance: 40
microsteps: 32
full_steps_per_rotation: 200
# Uncomment below if using direct inputs on Octo
#endstop_pin: ^PG10
# WAS for Huvud v0.5:
# endstop_pin: head1:PA1
endstop_pin: head1:PB10

position_min: -46.5
position_endstop: -46.25
position_max: 116

homing_speed: 50
homing_retract_dist: 3
second_homing_speed: 5
homing_positive_dir: false

[tmc2209 dual_carriage]
uart_pin: PC6
interpolate: false
run_current: 0.7
hold_current: 0.5
sense_resistor: 0.110
stealthchop_threshold: 500

##--------------------------------------------------------------------
##  Right Y motor (when looking at the front)
##  Connected to MOTOR_1
##  Endstop connected to DIAG_1
[stepper_y]
step_pin: PG0
dir_pin: PG1
enable_pin: !PF15
rotation_distance: 40
microsteps: 32
full_steps_per_rotation:200
endstop_pin: ^PG9
position_min: 0
position_endstop: 120
position_max: 120

homing_speed: 50  #Max 100
homing_retract_dist: 3
second_homing_speed: 5
homing_positive_dir: true

[tmc2209 stepper_y]
uart_pin: PD11
interpolate: false
run_current: 0.45
sense_resistor: 0.110
stealthchop_threshold: 500

##  Left Y motor (when looking at the front)
##  Connected to MOTOR_3
##  Endstop connected to DIAG_3
[stepper_y1]
step_pin: PG4
dir_pin: !PC1
enable_pin: !PA0
rotation_distance: 40
microsteps: 32
full_steps_per_rotation:200
endstop_pin: ^PG11

[tmc2209 stepper_y1]
uart_pin: PC7
interpolate: false
run_current: 0.45
sense_resistor: 0.110
stealthchop_threshold: 500

#####################################################################
#   Z Stepper Settings
#####################################################################
## Z0 Stepper - Front Right

##  Connected to MOTOR_4
##  Endstop connected to DIAG_4
[stepper_z]
step_pin: PF9
dir_pin: PF10
enable_pin: !PG2
rotation_distance: 32
microsteps: 64
endstop_pin: ^PG12

##  Z-position of nozzle (in mm) to z-endstop trigger point relative to print surface (Z0)
##  (+) value = endstop above Z0, (-) value = endstop below
##  Increasing position_endstop brings nozzle closer to the bed
##  After you run Z_ENDSTOP_CALIBRATE, position_endstop will be stored at the very end of your config
position_endstop: 0
position_max: 120

position_min: -5
homing_speed: 15
second_homing_speed: 3
homing_retract_dist: 2
homing_positive_dir: false

##  Make sure to update below for your relevant driver (2208 or 2209)
[tmc2209 stepper_z]
uart_pin: PF2
interpolate: false
run_current: 0.5
hold_current: 0.3
sense_resistor: 0.110
stealthchop_threshold: 500

## Z1 Stepper - Front Left
[stepper_z1]
step_pin: PC13
dir_pin: !PF0
enable_pin: !PF1
rotation_distance: 32
microsteps: 64

##	Make sure to update below for your relevant driver (2208 or 2209)
[tmc2209 stepper_z1]
uart_pin: PE4
interpolate: false
run_current: 0.5
hold_current: 0.3
sense_resistor: 0.110
stealthchop_threshold: 500

## Z2 Stepper - Rear
[stepper_z2]
step_pin: PE2
dir_pin: PE3
enable_pin: !PD4
rotation_distance: 32
microsteps: 64

##	Make sure to update below for your relevant driver (2208 or 2209)
[tmc2209 stepper_z2]
uart_pin: PE1
interpolate: false
run_current: 0.5
hold_current: 0.3
sense_resistor: 0.110
stealthchop_threshold: 500

#####################################################################
# Source for below: https://github.com/Klipper3d/klipper/blob/master/config/sample-idex.cfg#L5
#
# Manually merged with: https://github.com/charlespick/klipper/blob/work-dual-car-docs-20210721/config/sample-idex.cfg

# Helper script to park the carriage (called from T0 and T1 macros)
[gcode_macro PARK_extruder]
gcode:
    SAVE_GCODE_STATE NAME=park0
    G90
    G1 X168 F12000
    RESTORE_GCODE_STATE NAME=park0

# Activate the primary extruder
[gcode_macro T0]
variable_offset_applied: 0
gcode:
    {% set svv = printer.save_variables.variables %}
    {% if "x" in printer.toolhead.homed_axes %} # this check ensures compatibility with Cura
        PARK_{printer.toolhead.extruder}
    {% endif %}
    {% set fan_speed = printer["gcode_macro M106"].swap_speed %}
      {% if fan_speed != -1 %}
        SET_FAN_SPEED FAN=fan_extruder SPEED={fan_speed}
      {% else %}
        # Update core Klipper's fan speed to the fan speed of the active toolhead
        # Only do this if you have a sacrificial [fan] section
        #M106.1 S{printer["fan_generic fan_extruder"].speed * 255}
    {% endif %}
    ACTIVATE_EXTRUDER EXTRUDER=extruder
    SET_DUAL_CARRIAGE CARRIAGE=0
    {% if printer["gcode_macro T0"].offset_applied == 1 %}
        SET_GCODE_OFFSET  X_ADJUST={ -(svv.xoffset) } Y_ADJUST={ -(svv.yoffset) }
        SET_GCODE_OFFSET Z_ADJUST={ -(svv.zoffset) } MOVE=1
        SET_GCODE_VARIABLE MACRO=T0 VARIABLE=offset_applied VALUE=0
    {% endif %}
#    SET_INPUT_SHAPER if necessary, reset the input shaper after using the second extruder

[gcode_macro PARK_extruder1]
gcode:
    SAVE_GCODE_STATE NAME=park1
    G90
    G1 X-46 F12000
    RESTORE_GCODE_STATE NAME=park1

[gcode_macro T1]
gcode:
    {% set svv = printer.save_variables.variables %}
    {% if "x" in printer.toolhead.homed_axes %} # this check ensures compatibility with Cura
        PARK_{printer.toolhead.extruder}
    {% endif %}
    {% set fan_speed = printer["gcode_macro M106"].swap_speed %}
      {% if fan_speed != -1 %}
        SET_FAN_SPEED FAN=fan_extruder1 SPEED={fan_speed}
      {% else %}
        # Update core Klipper's fan speed to the fan speed of the active toolhead
        # Only do this if you have a sacrificial [fan] section
        #M106.1 S{printer["fan_generic fan_extruder1"].speed * 255}
    {% endif %}
    ACTIVATE_EXTRUDER EXTRUDER=extruder1
    SET_DUAL_CARRIAGE CARRIAGE=1
    {% if printer["gcode_macro T0"].offset_applied == 0 %}
        SET_GCODE_OFFSET  X_ADJUST={ svv.xoffset } Y_ADJUST={ svv.yoffset }
        SET_GCODE_OFFSET Z_ADJUST={ svv.zoffset } MOVE=1
        SET_GCODE_VARIABLE MACRO=T0 VARIABLE=offset_applied VALUE=1
    {% endif %}
#    SET_INPUT_SHAPER if necessary, update input shaping for the second carraige
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

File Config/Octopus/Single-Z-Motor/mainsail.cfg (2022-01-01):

# [virtual_sdcard]
# path: /home/pi/gcode_files

# [pause_resume]

# [display_status]

# [gcode_macro CANCEL_PRINT]
# rename_existing: BASE_CANCEL_PRINT
# gcode:
#     TURN_OFF_HEATERS
#     CLEAR_PAUSE
#     SDCARD_RESET_FILE
#     BASE_CANCEL_PRINT

[virtual_sdcard]
path: /home/pi/gcode_files

[pause_resume]

[display_status]

[gcode_macro CANCEL_PRINT]
description: Cancel the actual running print
rename_existing: CANCEL_PRINT_BASE
gcode:
    TURN_OFF_HEATERS
    CANCEL_PRINT_BASE

[gcode_macro PAUSE]
description: Pause the actual running print
rename_existing: PAUSE_BASE
# change this if you need more or less extrusion
variable_extrude: 1.0
gcode:
    ##### read E from pause macro #####
    {% set E = printer["gcode_macro PAUSE"].extrude|float %}
    ##### set park positon for x and y #####
    # default is your max posion from your printer.cfg
    {% set x_park = printer.toolhead.axis_maximum.x|float - 5.0 %}
    {% set y_park = printer.toolhead.axis_maximum.y|float - 5.0 %}
    ##### calculate save lift position #####
    {% set max_z = printer.toolhead.axis_maximum.z|float %}
    {% set act_z = printer.toolhead.position.z|float %}
    {% if act_z < (max_z - 2.0) %}
        {% set z_safe = 2.0 %}
    {% else %}
        {% set z_safe = max_z - act_z %}
    {% endif %}
    ##### end of definitions #####
    PAUSE_BASE
    G91
    {% if printer.extruder.can_extrude|lower == 'true' %}
      G1 E-{E} F2100
    {% else %}
      {action_respond_info("Extruder not hot enough")}
    {% endif %}
    {% if "xyz" in printer.toolhead.homed_axes %}
      G1 Z{z_safe} F900
      G90
      G1 X{x_park} Y{y_park} F6000
    {% else %}
      {action_respond_info("Printer not homed")}
    {% endif %} 
    
[gcode_macro RESUME]
description: Resume the actual running print
rename_existing: RESUME_BASE
gcode:
    ##### read E from pause macro #####
    {% set E = printer["gcode_macro PAUSE"].extrude|float %}
    #### get VELOCITY parameter if specified ####
    {% if 'VELOCITY' in params|upper %}
      {% set get_params = ('VELOCITY=' + params.VELOCITY)  %}
    {%else %}
      {% set get_params = "" %}
    {% endif %}
    ##### end of definitions #####
    {% if printer.extruder.can_extrude|lower == 'true' %}
      G91
      G1 E{E} F2100
    {% else %}
      {action_respond_info("Extruder not hot enough")}
    {% endif %}  
    RESUME_BASE {get_params}

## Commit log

2022-01-01 Alpha-1 Release
    World's smallest IDEX.
    Enjoy,
    -Z
    [Cable_Channel_100mm_15x22_Base_x3.stl, Cable_Channel_100mm_15x22_Cover_x3.stl, Huvud_Motor_Spacer_x4.stl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]
2022-01-04 Update README and add pic of print
2022-04-21 Add doublewide 'Dragon Bed' - UNTESTED
    [Dragon_Bed.f3d, Dragon_Bed.step, Dragon_Bed_Assembly.f3z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]
2022-05-20 Add latest T0+2xHuvud configs
    [builtin_extruder0.cfg, builtin_extruder1.cfg, mainsail.cfg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]
2022-05-21 Fix typo in macro
    Thanks BeastBC for the pointer.
    [printer.cfg]
2022-06-19 Add updated Dragon Beds
    Now available, with magnets, by Mandala Rose Works
    [Dragon_Bed.f3d, Dragon_Bed.step, Dragon_Bed_200.f3d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]
2022-06-19 Reomve out-of-date Dragon Bed files
    [Dragon_Bed_Assembly.f3z, Dragon_Bed_Assembly.step, Dragon_Bed_Rectangular.step]
